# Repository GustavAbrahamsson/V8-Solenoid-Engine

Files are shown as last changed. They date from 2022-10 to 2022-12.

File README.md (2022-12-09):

# V8-Solenoid-Engine

See it in action:

https://imgur.com/a/upsOSZD

https://imgur.com/a/mojqysO

https://imgur.com/a/09qQa0Y

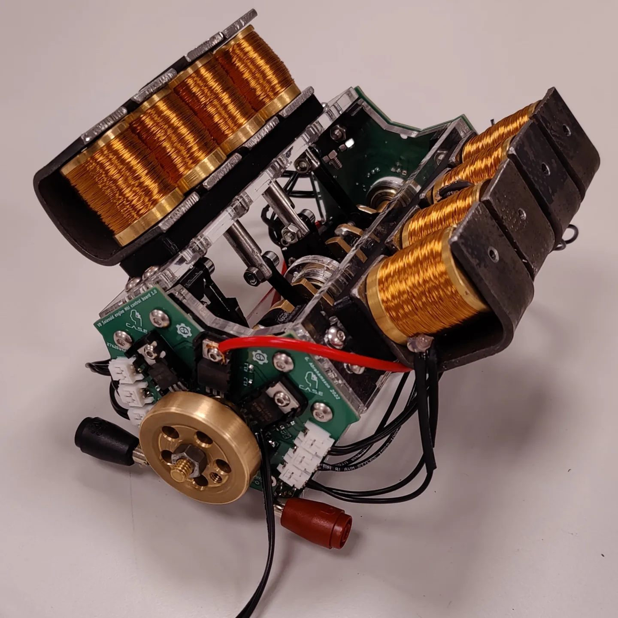
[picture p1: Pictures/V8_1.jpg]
 
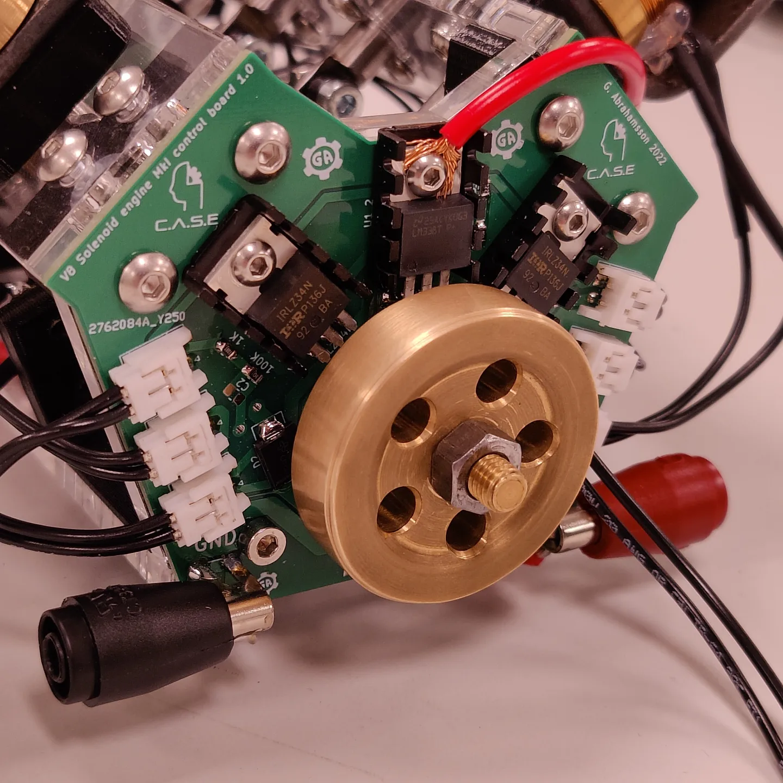
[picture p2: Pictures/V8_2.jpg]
 
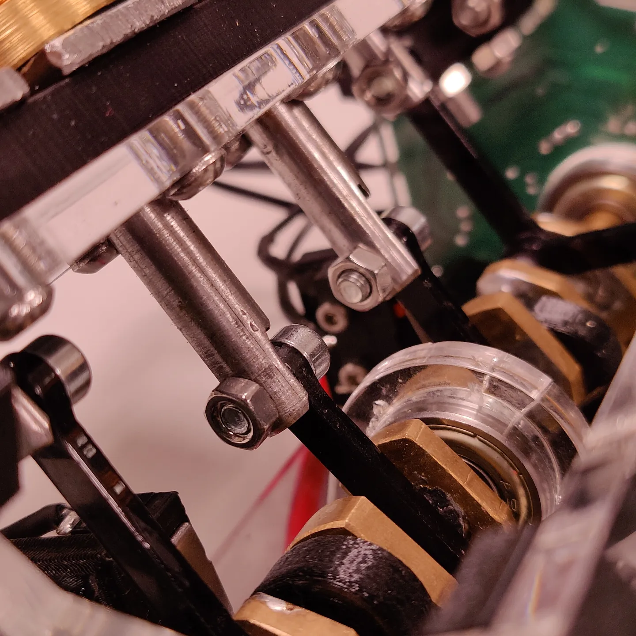
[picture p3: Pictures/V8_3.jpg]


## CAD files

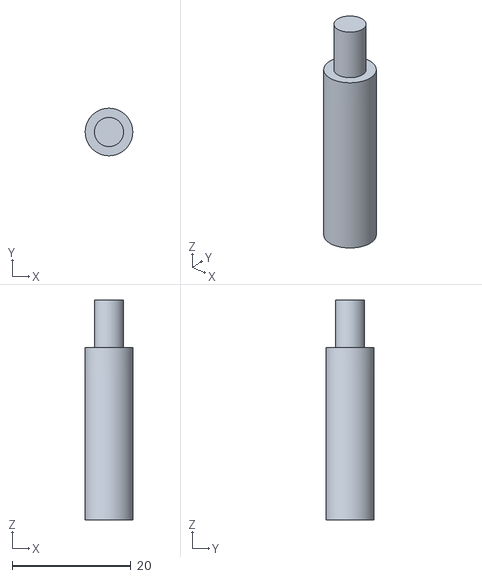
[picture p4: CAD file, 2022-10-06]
CAD/Main axle.stl
8.00 x 8.00 x 37.0

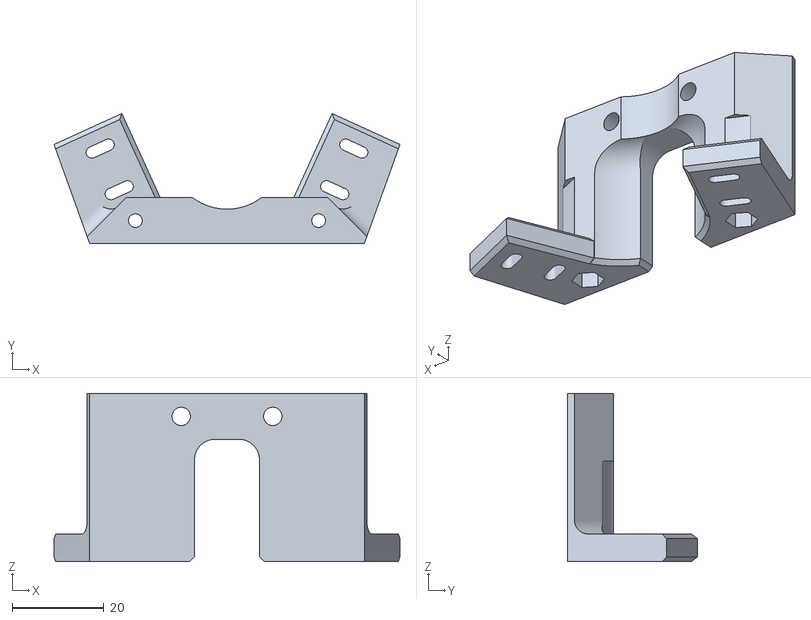
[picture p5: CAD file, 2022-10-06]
CAD/1.1/Front mount1_1.stl
75.6 x 28.4 x 36.7

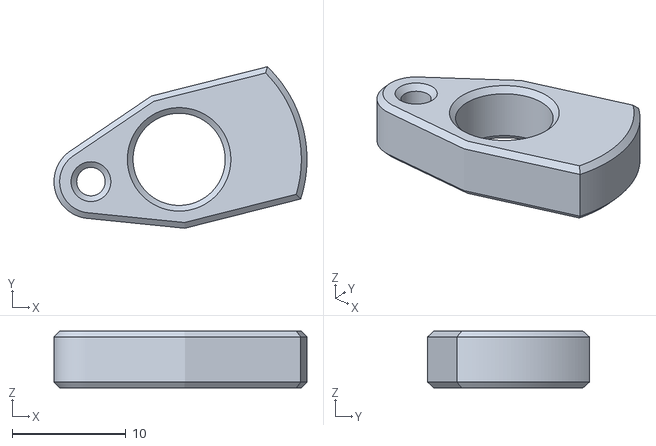
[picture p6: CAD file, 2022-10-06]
CAD/Crank 1.0.stl
22.3 x 14.2 x 5.00

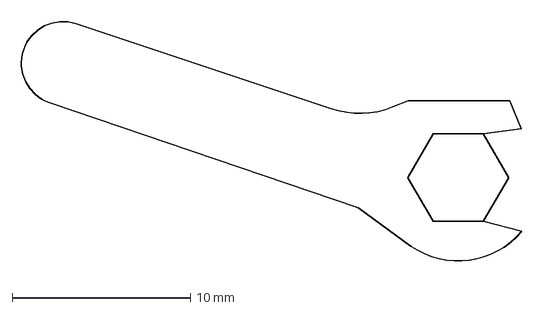
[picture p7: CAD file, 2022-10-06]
CAD/Tools/m2dot5.dxf
28.4 x 14.3 mm

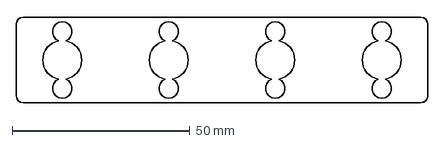
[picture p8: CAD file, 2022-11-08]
DXF/1.1/solenoid distance plate (3mm).dxf
116.0 x 24.0 mm

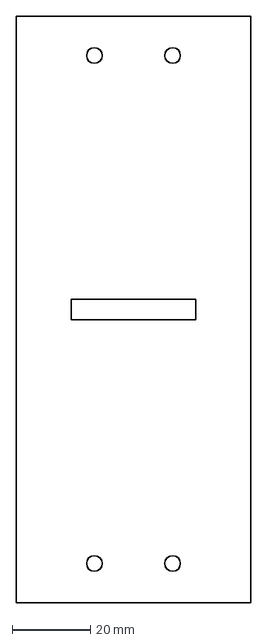
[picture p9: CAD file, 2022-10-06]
DXF/Bottom plate 1.0 5 mm.dxf
60.0 x 150.0 mm

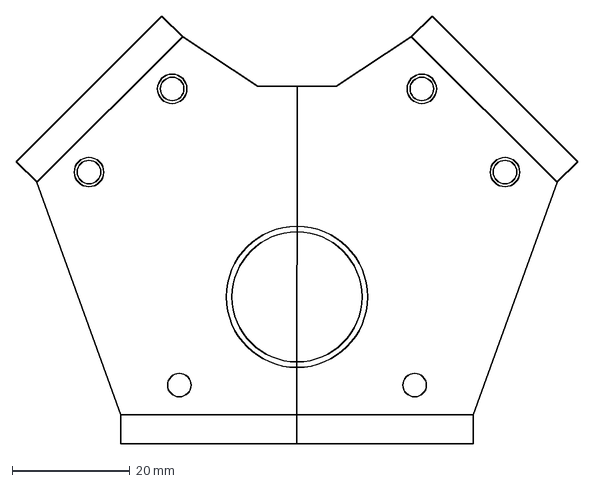
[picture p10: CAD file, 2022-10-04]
Electronics/PCB 1.0/frontSilouette.dxf
95.5 x 72.7 mm

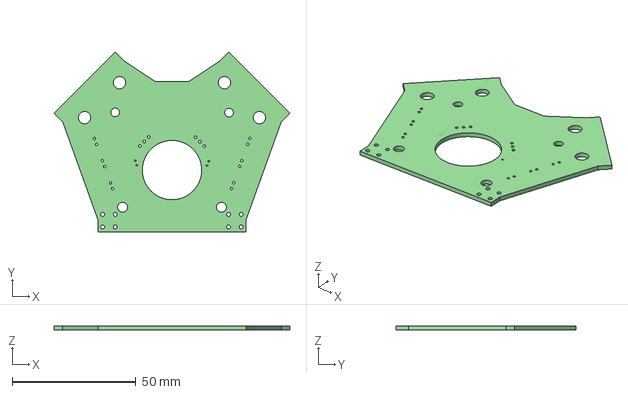
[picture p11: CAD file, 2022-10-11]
Electronics/PCB 1.0/V8_controller1.0/V8_controller1.0.step
95.5 x 72.7 x 1.60 mm

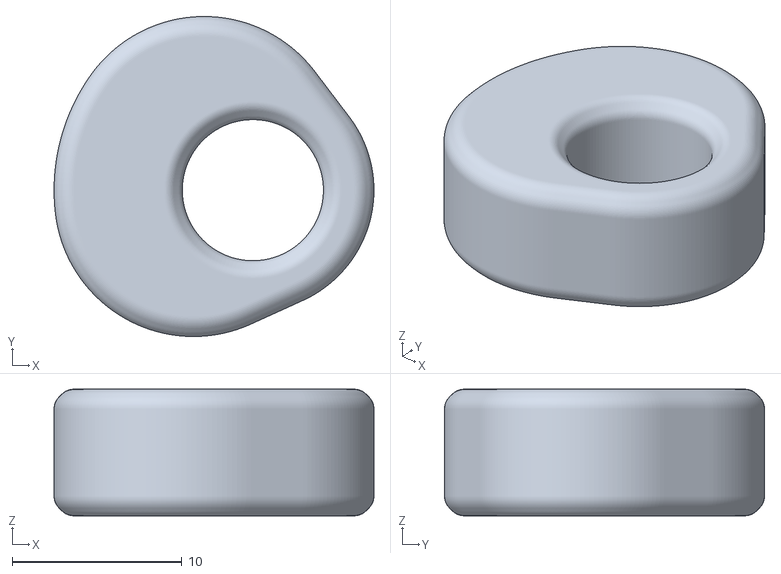
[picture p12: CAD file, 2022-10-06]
CAD/1.1/Cam1_1.stl
18.8 x 18.8 x 7.45

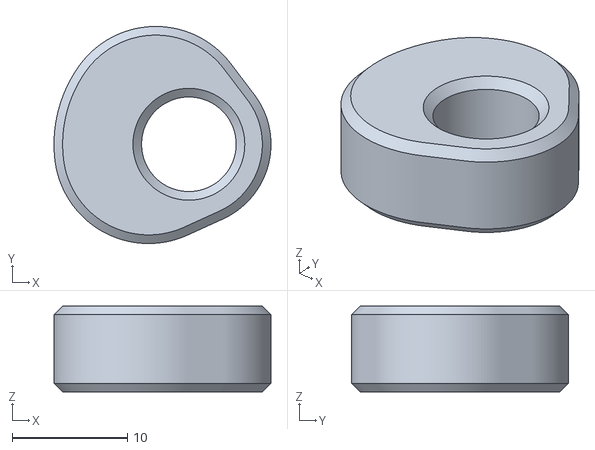
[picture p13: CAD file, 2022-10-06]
CAD/Cam.stl
18.8 x 18.8 x 7.45

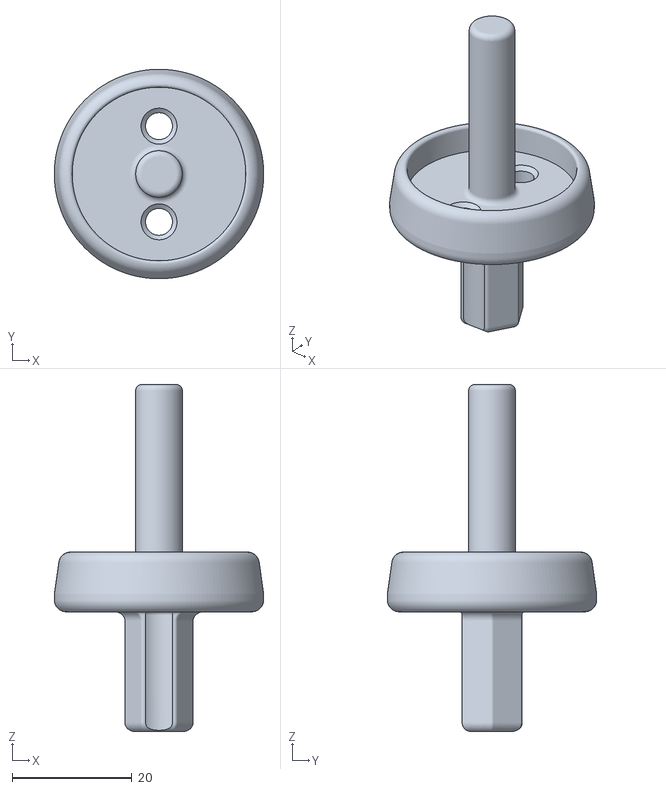
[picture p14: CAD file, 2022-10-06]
CAD/Tools/Coil winder.stl
35.0 x 35.0 x 58.0

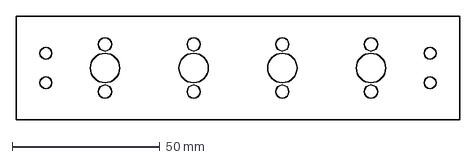
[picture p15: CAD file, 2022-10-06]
DXF/1.1/sideplate1_1.dxf
150.0 x 35.0 mm

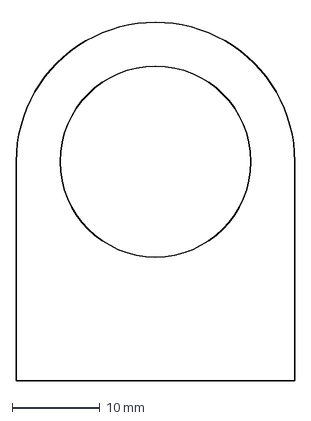
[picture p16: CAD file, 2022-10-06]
DXF/Bearing holder 1.0_6mm.dxf
31.7 x 41.6 mm

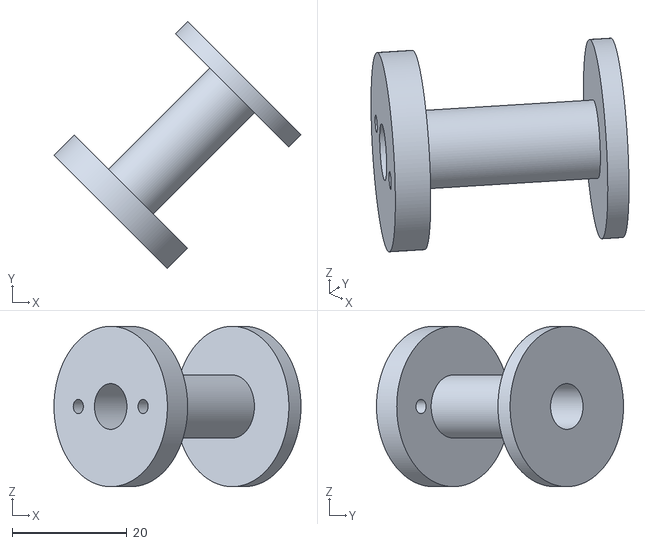
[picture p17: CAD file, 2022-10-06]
CAD/Cylinder 1.0.stl
43.1 x 43.1 x 28.0

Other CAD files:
DXF/1.1/linkarm.dxf
DXF/Front plate 1.0 5mm.dxf
CAD/Body17.stl
DXF/Link arm 1.0_5mm.dxf
CAD/CornerMount 1.0.stl
CAD/Crank rod.stl
CAD/Front mount 1.0.stl
CAD/Piston 1.0.stl
DXF/Bearing fit test.dxf
DXF/Side plate 1.0 6mm.dxf

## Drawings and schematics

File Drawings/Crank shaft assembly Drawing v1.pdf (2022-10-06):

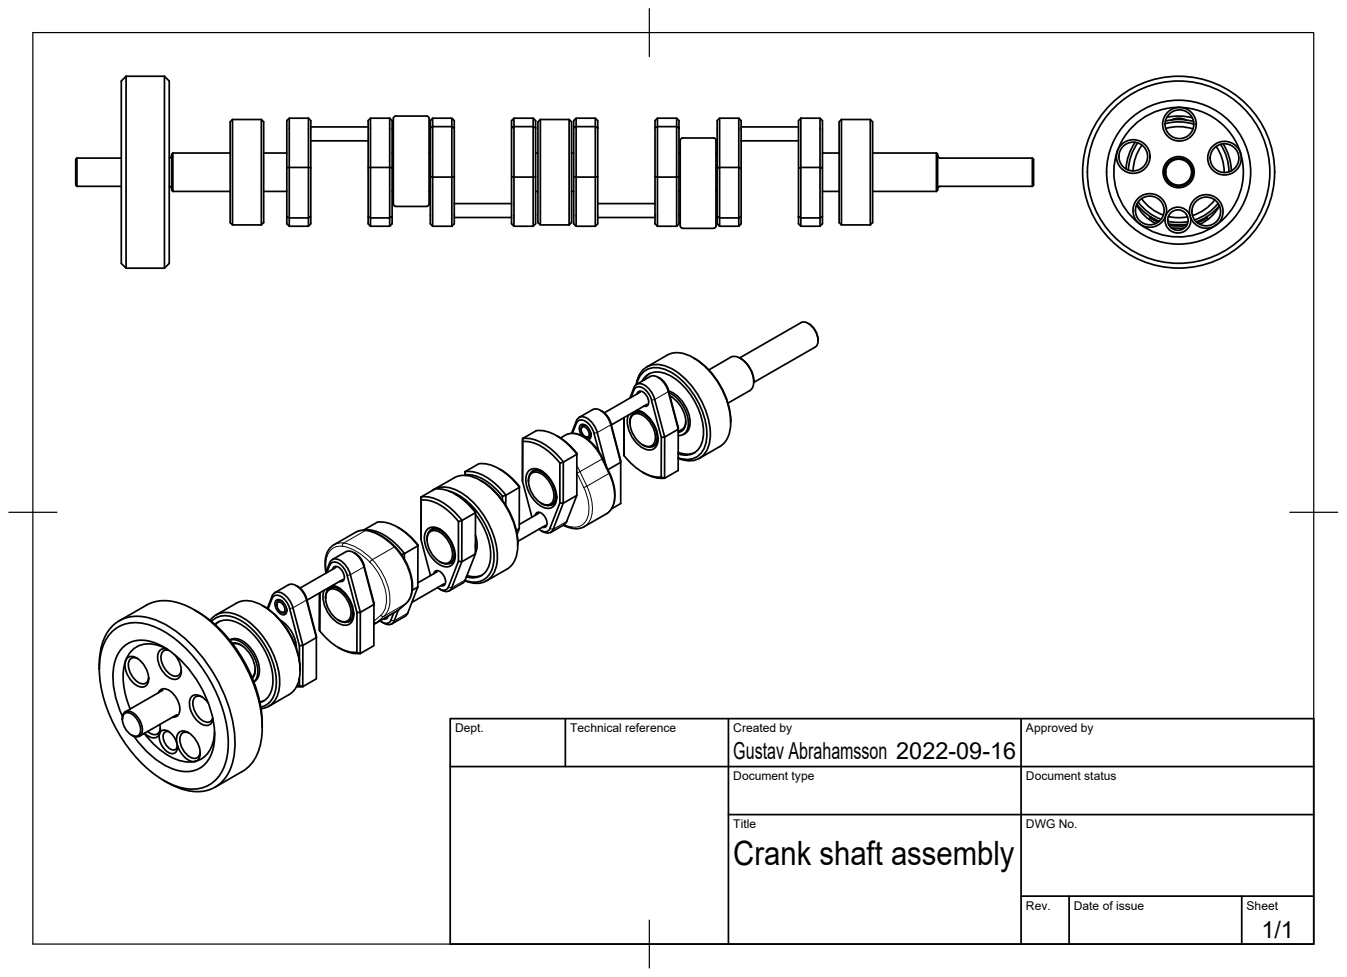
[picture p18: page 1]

Dept. | Technical reference | Created by Gustav Abrahamsson 2022-09-16 | Approved by

Document type | Document status

Title Crank shaft assembly | DWG No.

Rev. | Date of issue | Sheet 1/1

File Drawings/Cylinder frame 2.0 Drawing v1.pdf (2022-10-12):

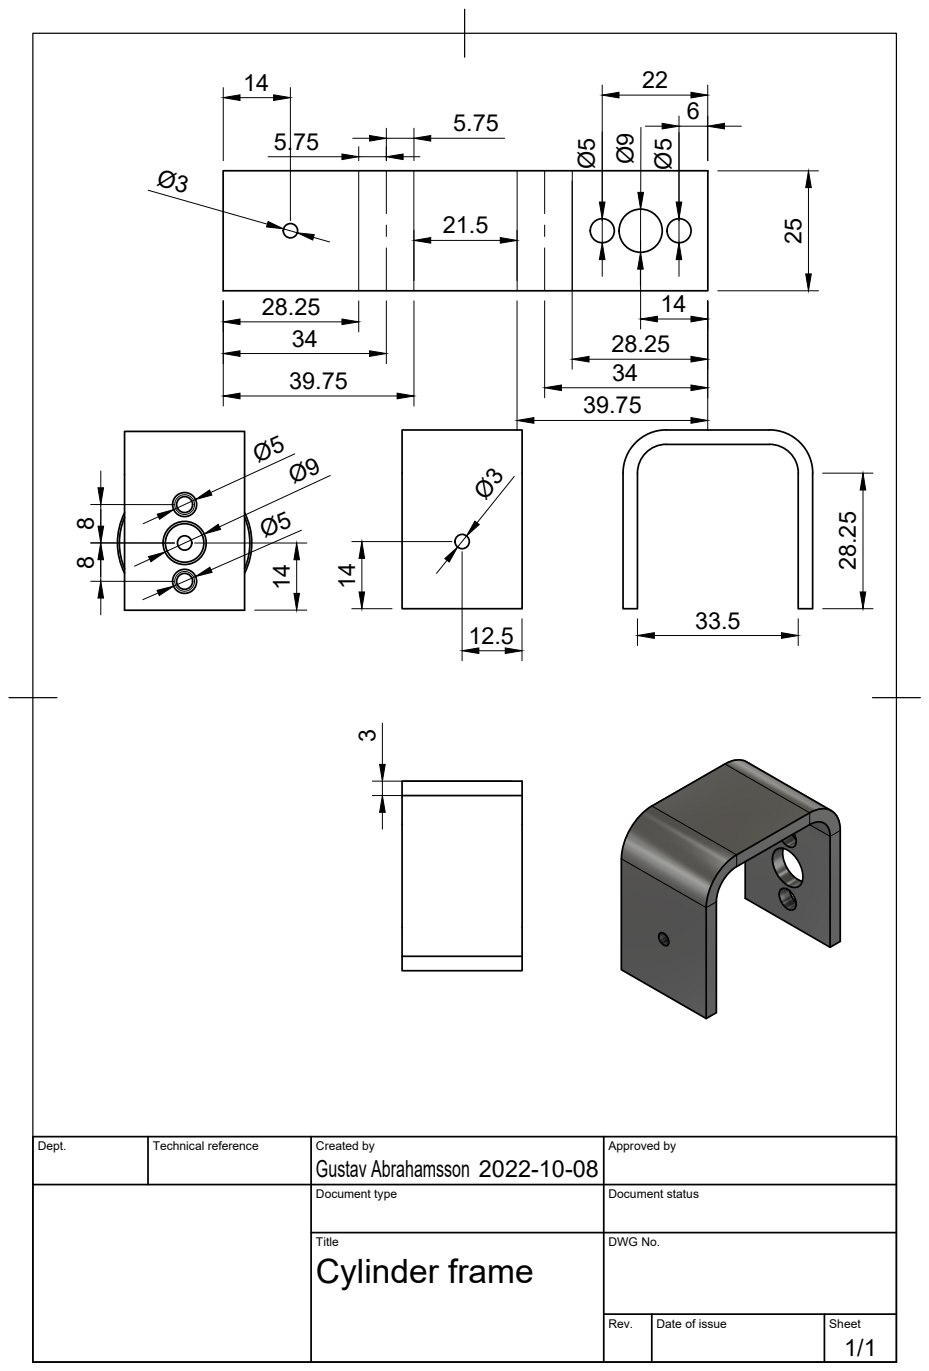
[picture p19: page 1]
Gustav Abrahamsson 14

Dept. | Technical reference | Created by 2022-10-08 | Approved by

Document type | Document status

Title Cylinder frame | DWG No.

Rev. | Date of issue | Sheet 1/1

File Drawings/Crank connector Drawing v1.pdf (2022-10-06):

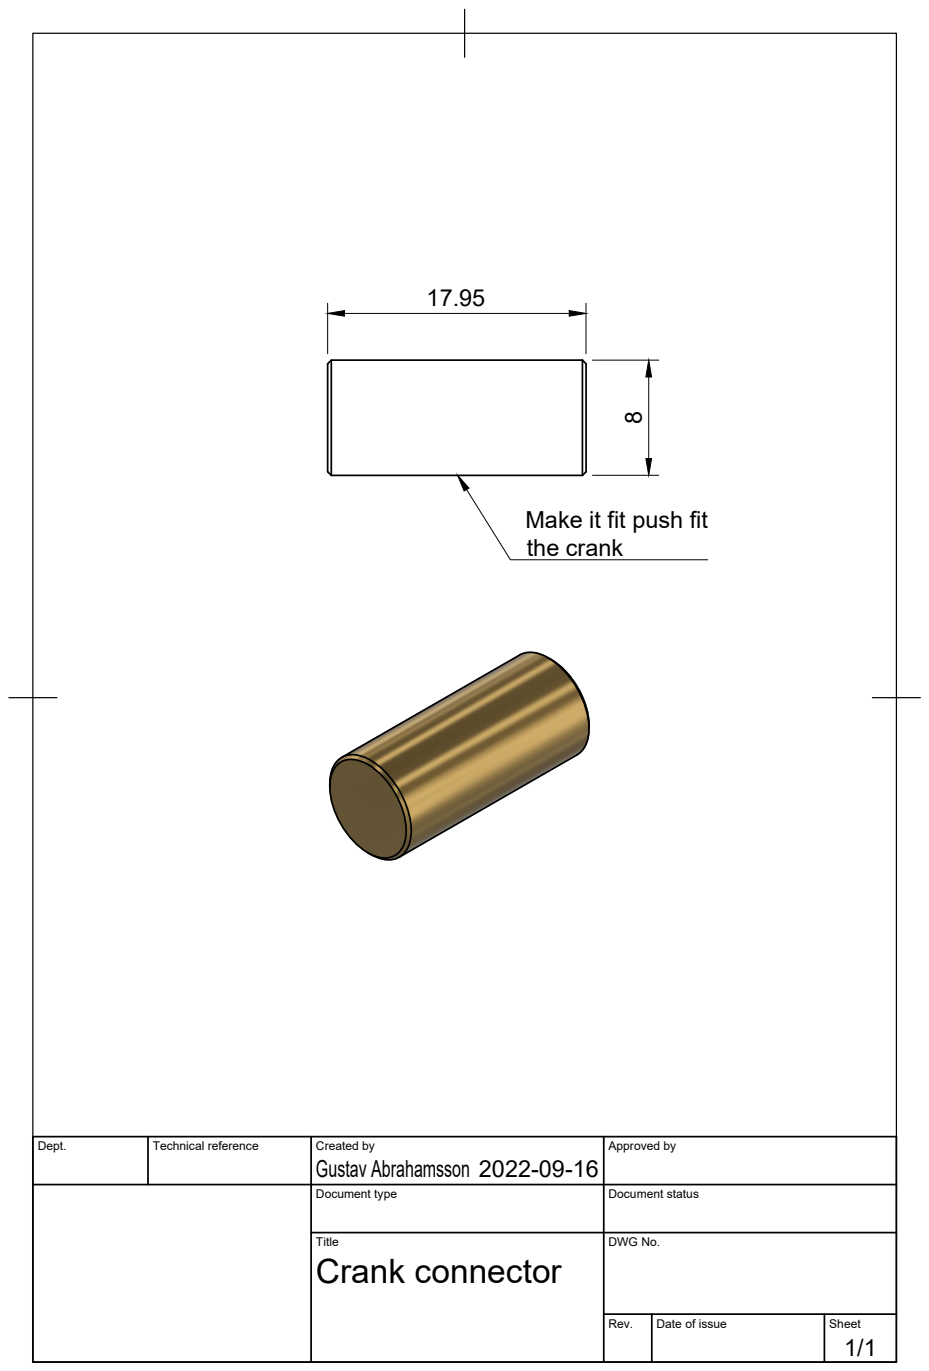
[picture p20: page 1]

Make it fit push fit
the crank

Dept. | Technical reference | Created by Gustav Abrahamsson 2022-09-16 | Approved by

Document type | Document status

Title Crank connector | DWG No.

Rev. | Date of issue | Sheet 1/1

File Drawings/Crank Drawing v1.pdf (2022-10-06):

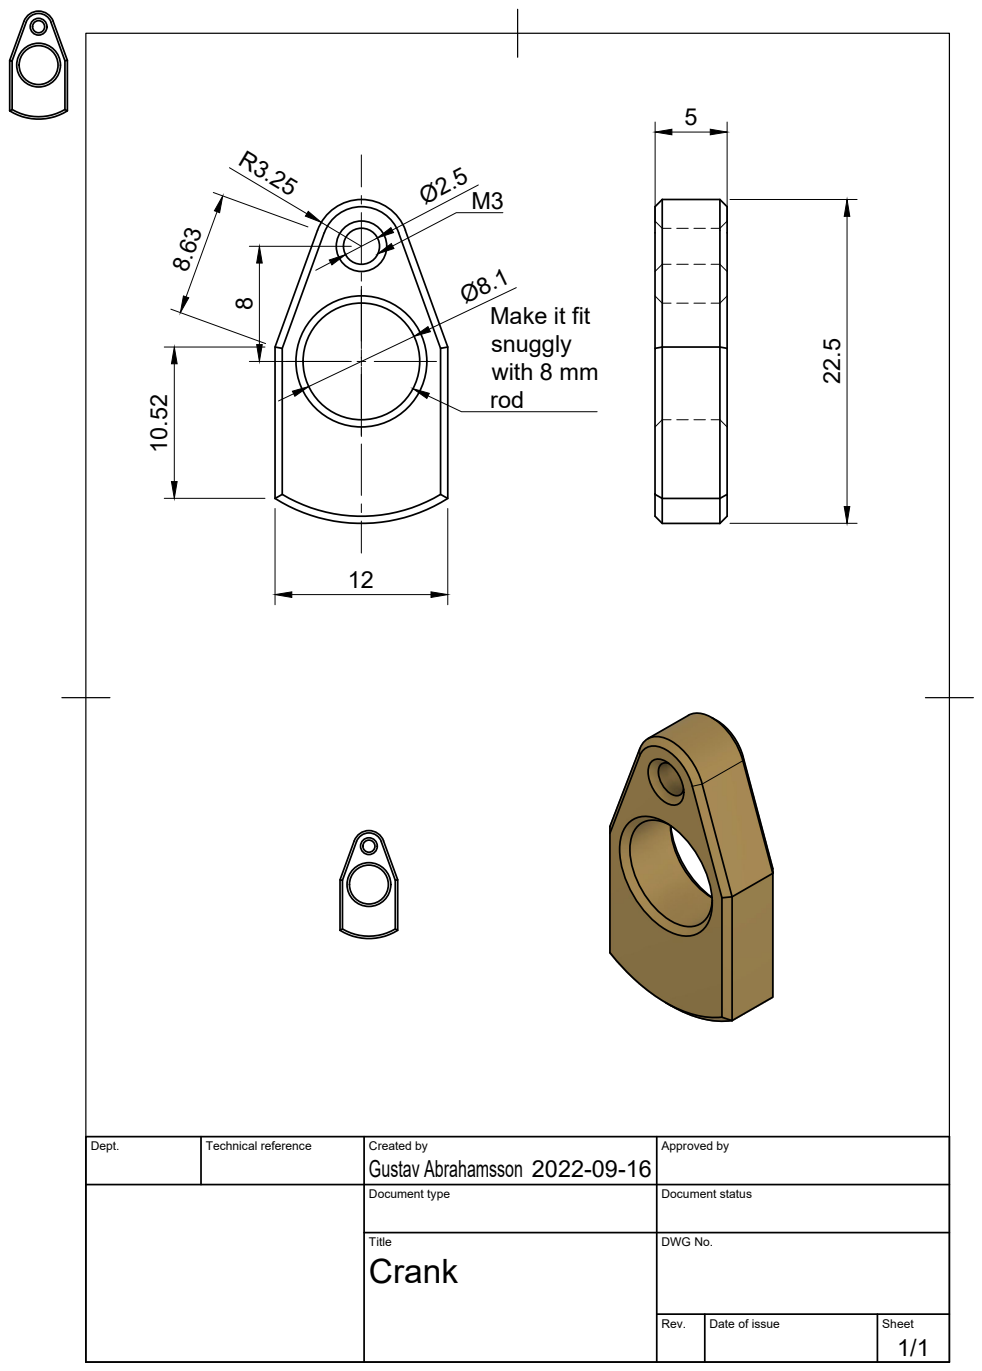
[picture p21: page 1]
Gustav Abrahamsson

Make it fit
snuggly
with 8 mm
rod

Dept. | Technical reference | Created by 2022-09-16 | Approved by

Document type | Document status

Title Crank | DWG No.

Rev. | Date of issue | Sheet 1/1

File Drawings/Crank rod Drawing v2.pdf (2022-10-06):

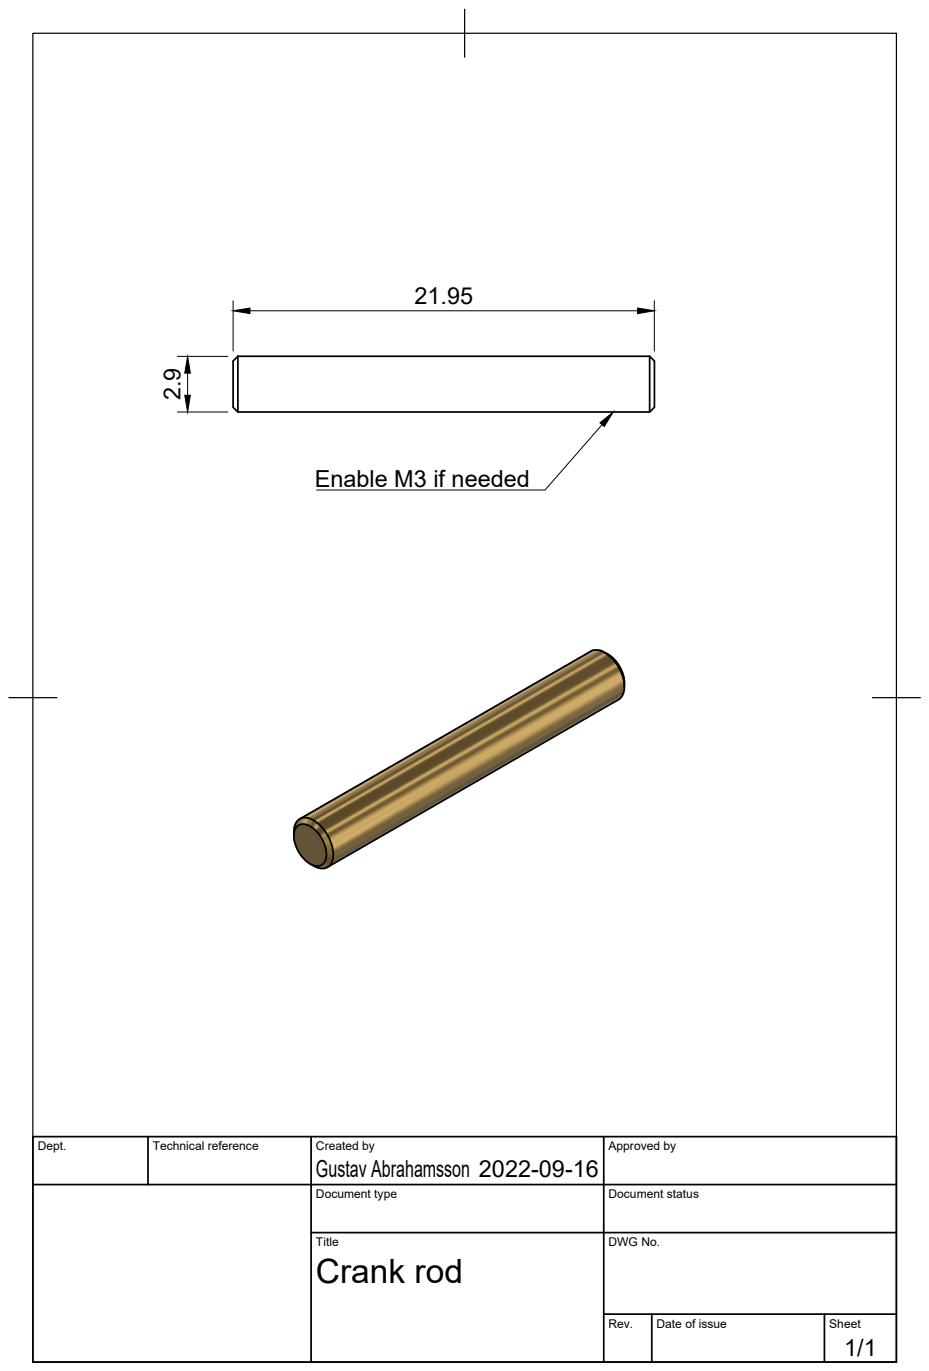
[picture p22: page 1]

Enable M3 if needed

Dept. | Technical reference | Created by Gustav Abrahamsson 2022-09-16 | Approved by

Document type | Document status

Title Crank rod | DWG No.

Rev. | Date of issue | Sheet 1/1

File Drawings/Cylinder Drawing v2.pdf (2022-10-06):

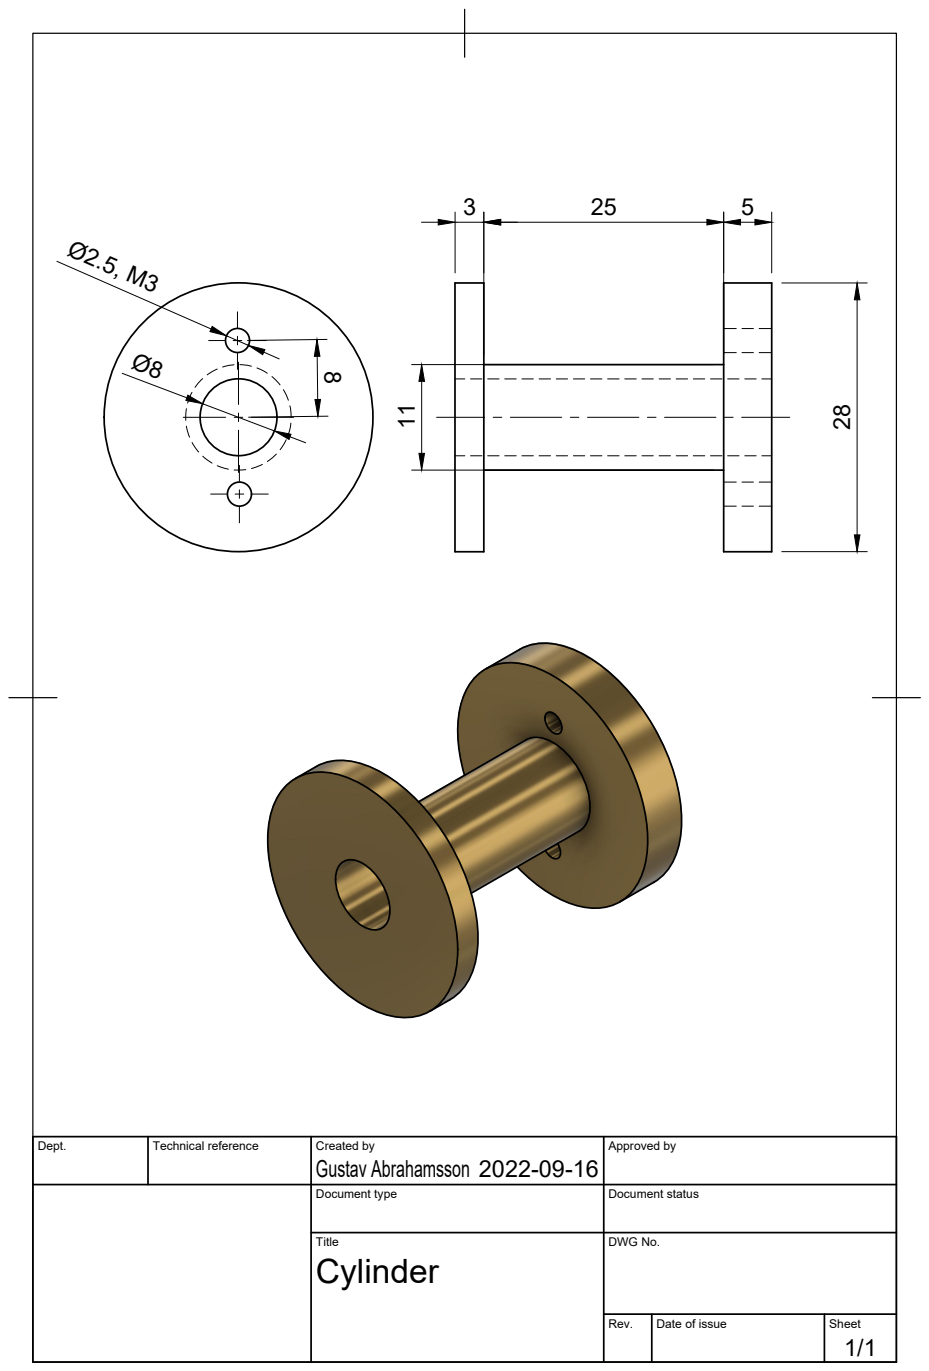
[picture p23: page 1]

Dept. | Technical reference | Created by Gustav Abrahamsson 2022-09-16 | Approved by

Document type | Document status

Title Cylinder | DWG No.

Rev. | Date of issue | Sheet 1/1

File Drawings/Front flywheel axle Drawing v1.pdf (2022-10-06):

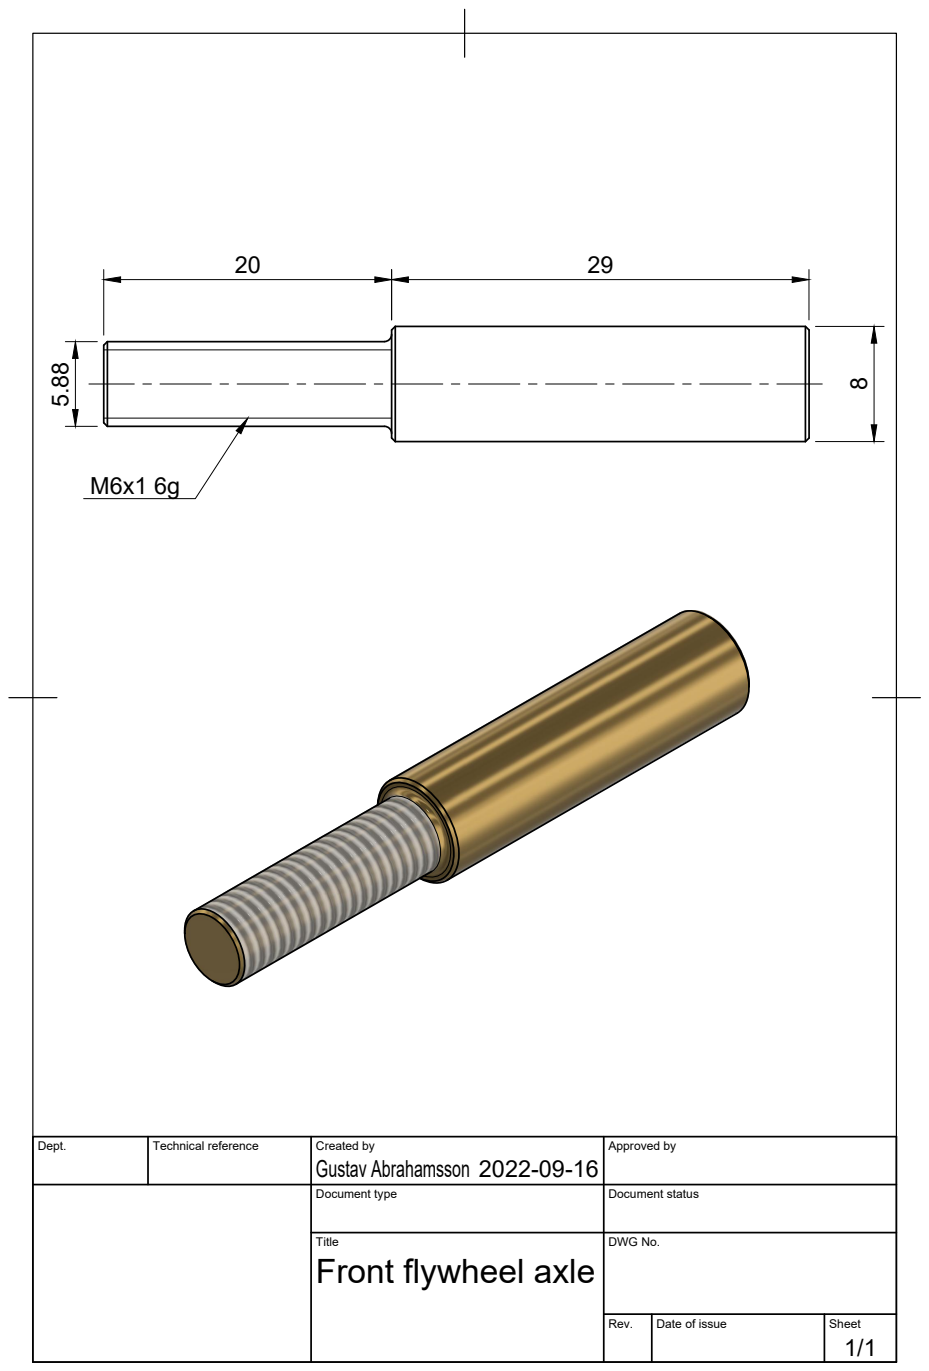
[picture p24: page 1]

Dept. | Technical reference | Created by Gustav Abrahamsson 2022-09-16 | Approved by

Document type | Document status

Title Front flywheel axle | DWG No.

Rev. | Date of issue | Sheet 1/1

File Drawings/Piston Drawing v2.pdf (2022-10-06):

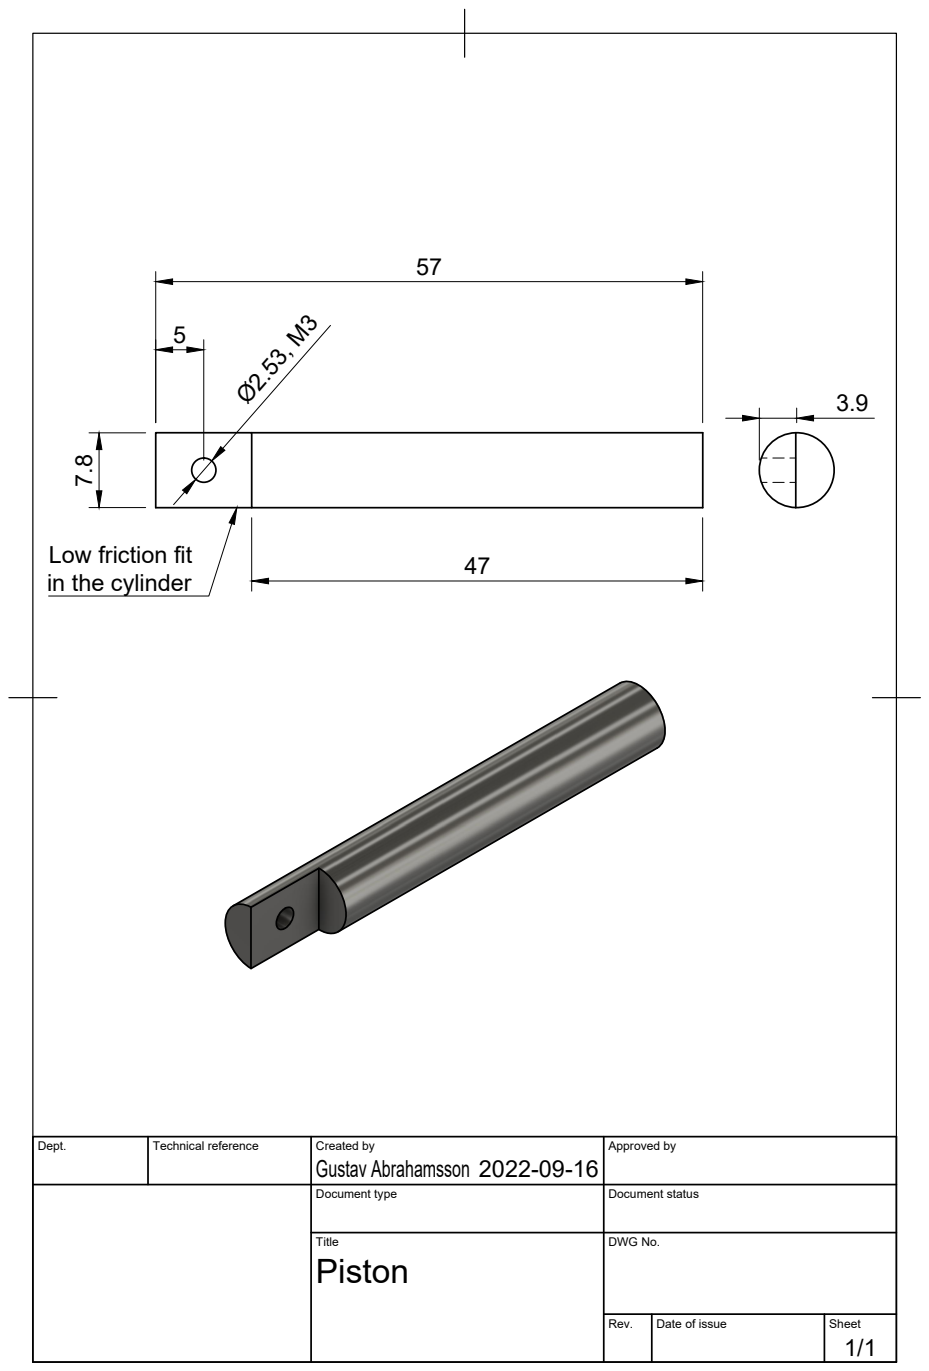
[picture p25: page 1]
Gustav Abrahamsson 7.8

Low friction fit
in the cylinder

Dept. | Technical reference | Created by 2022-09-16 | Approved by

Document type | Document status

Title Piston | DWG No.

Rev. | Date of issue | Sheet 1/1

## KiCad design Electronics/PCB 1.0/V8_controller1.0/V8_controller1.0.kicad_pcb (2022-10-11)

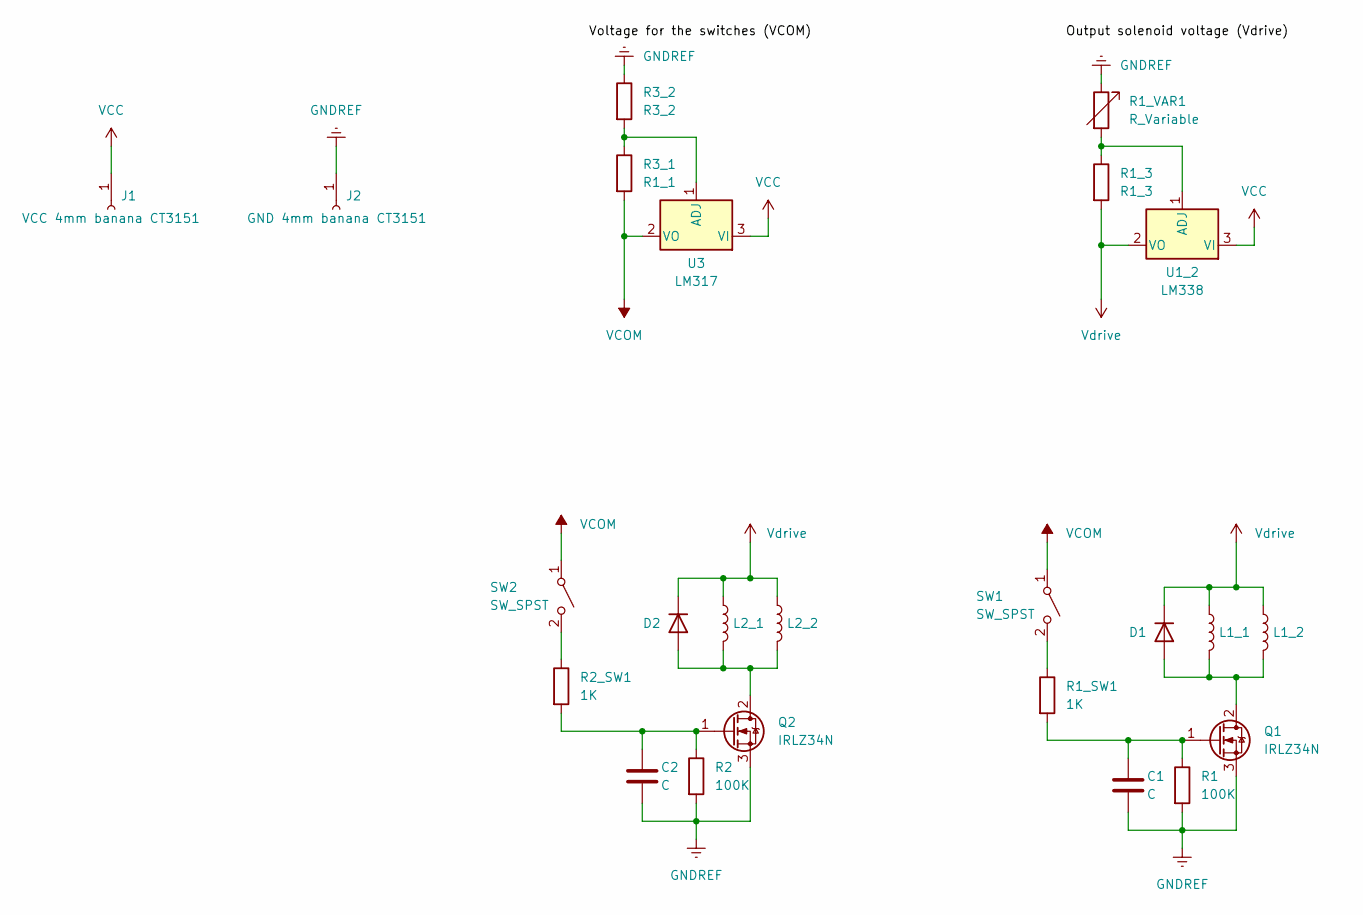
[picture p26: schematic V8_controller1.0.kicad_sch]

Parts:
C1, C2: C; R_0805_2012Metric_Pad1.20x1.40mm_HandSolder
D1, D2: DIODE; D_SMA-SMB_Universal_Handsoldering
J1: VCC 4mm banana CT3151; CalTest_CT3151
J2: GND 4mm banana CT3151; CalTest_CT3151
L1_1, L1_2, L2_1, L2_2: L; JST_EH_S2B-EH_1x02_P2.50mm_Horizontal
Q1, Q2: IRLZ34N; TO-220-3_Horizontal_TabDown
R1, R2: 100K; R_0805_2012Metric_Pad1.20x1.40mm_HandSolder
R1_3: R1_3; R_0805_2012Metric_Pad1.20x1.40mm_HandSolder
R1_SW1, R2_SW1: 1K; R_0805_2012Metric_Pad1.20x1.40mm_HandSolder
R1_VAR1: R_Variable; R_Axial_DIN0204_L3.6mm_D1.6mm_P1.90mm_Vertical
R3_1: R1_1; R_0805_2012Metric_Pad1.20x1.40mm_HandSolder
R3_2: R3_2; R_0805_2012Metric_Pad1.20x1.40mm_HandSolder
SW1, SW2: SW_SPST; JST_EH_S2B-EH_1x02_P2.50mm_Horizontal
U1_2: LM338; TO-220-3_Horizontal_TabDown
U3: LM317; TO-263-2

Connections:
GNDREF: C1.2, C2.2, J2.1, Q1.3 (S), Q2.3 (S), R1.2, R1_VAR1.1, R2.2, R3_2.1
unnamed: C1.1, Q1.1 (G), R1.1, R1_SW1.2
unnamed: C2.1, Q2.1 (G), R2.1, R2_SW1.2
unnamed: D1.1 (A), L1_1.2, L1_2.2, Q1.2 (D)
unnamed: D2.1 (A), L2_1.2, L2_2.2, Q2.2 (D)
unnamed: R1_3.1, R1_VAR1.2, U1_2.1 (ADJ)
unnamed: R1_SW1.1, SW1.2 (B)
unnamed: R2_SW1.1, SW2.2 (B)
unnamed: R3_1.1, R3_2.2, U3.1 (ADJ)
VCC: J1.1, U1_2.3 (VI), U3.3 (VI)
VCOM: R3_1.2, SW1.1 (A), SW2.1 (A), U3.2 (VO)
Vdrive: D1.2 (K), D2.2 (K), L1_1.1, L1_2.1, L2_1.1, L2_2.1, R1_3.2, U1_2.2 (VO)

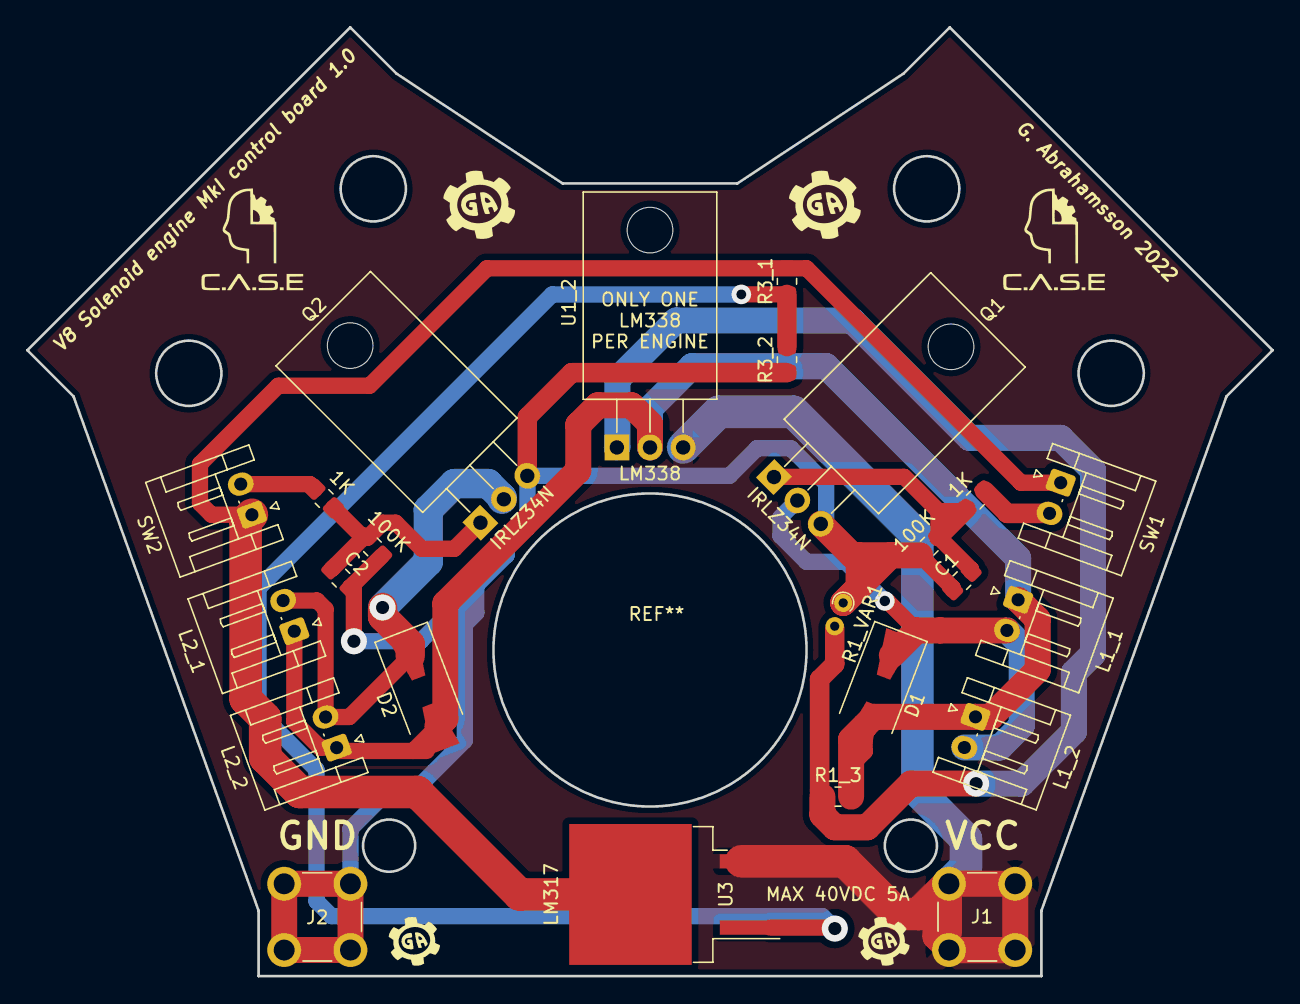
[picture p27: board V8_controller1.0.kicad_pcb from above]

Board: 2 copper layers, 95.5 x 72.7 mm, 24 parts (0 on the bottom side), 12 nets.

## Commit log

2022-10-04 Add KiCad project
    [V8_controller1.0.kicad_pcb, V8_controller1.0.kicad_sch, frontSilouette.dxf]
2022-10-05 Add voltage control with extra LM317
    [V8_controller1.0.kicad_sch]
2022-10-06 Add CAD
    [Bearing holder 1.0_6mm.dxf, Body17.stl, Bottom plate 1.0 5 mm.dxf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]
2022-10-11 Add final gerberfiles for 1.0
    [V8_controller1.0-B_Cu.gbr, V8_controller1.0-B_Mask.gbr, V8_controller1.0-B_Paste.gbr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]
2022-10-12 Add updated cylinder frame drawing
2022-11-08 Update improvements
    [solenoid distance plate (3mm).dxf]
